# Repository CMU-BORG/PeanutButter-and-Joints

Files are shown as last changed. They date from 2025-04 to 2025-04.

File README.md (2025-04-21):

# PeanutButter-and-Joints
Paper: "PB&J: Peanut Butter and Joints for Damped Articulation"

An open-source, low-cost, biomimetic robotic grasper platform modeled on the human hand, incorporating the effects of viscoelastic joint mechanics.

An archived version of this repository is available through Zenodo:  

Authors:

* Avery S. Williamson<sup>+</sup>
* Michael J. Bennington<sup>+</sup>
* Ravesh Sukhnandan<sup>+</sup>
* Mrinali Nakhre
* Yeumin Mao
* Victoria A. Webster-Wood

<i>All authors are affiliated with Carnegie Mellon University</i>

+: These authors contributed equally to this manuscript.

This repository serves as the home for the open-source Peanut Butter and Joints biomimetic robotic grasper. The design, modeling, and characterization of this grasper is detailed in the manuscript references above. This repository contains the design files (SolidWorks part and assembly files, STLs for 3D printed components, and engineering drawings (limited) ), simulation files and associated code, and experimental data associated with the above manuscript. 

> [!NOTE]
> If you are interesting in utilizing or modifying this grasper or any of its subcomponents for your own <i>in roboto</i> investigations of human like grasping or robotic grasper development, please cite using the following DOI:
>  
> <b>Above will to be updated with correct DOI upon publication</b>
>
> Williamson, Bennington, and Sukhnandan, <i>et al.</i>, "PB&J: Peanut Butter and Joints for Damped Articulation." (2025).

## Overview:

The files in the repository are organized into three subdirectories:

- Arduino Controller

- CAD

- Modeling and Experimental Data

### Directory: [Arduino Controller](https://github.com/CMU-BORG/PeanutButter-and-Joints/tree/main/Arduino%20Controller)
This directory contains a folder entitled "Code Files" which hold all files required to implement the position controller described in the manuscript. 
 - "DCMotor.cpp" and "DCMotor.h" are library files which provide code to interface with the motor that actuates the hand.
 - "handrobot.ino" is the main Arduino/Teensy code file that implements the controller and can be used to conduct the ball drop tests.
 
### Directory: [CAD](https://github.com/CMU-BORG/PeanutButter-and-Joints/tree/main/CAD)
This directory contains the SolidWorks part files, STL files, and engineering drawings associated with the grasper and its various subcomponents. Each of these folders is further organized by the subsystem to which the files belong.
 - "Hand:" files associated with the 3D printed hand, including the palm, phalanges, and encoder mounts.
 - "Damper:" files associated with the concentric ring viscous damper (peanut butter not included)
 - "Hand Stand:" files associated with the experimental test stand used to folder the grasper in place during drop tests.
 - "Ball Stand:" files associated with the experimental test stand use to hold the ball servo and laser distance sensor used during ball drop tests.
 - "Misc:" miscellanious files associated with other components of the hand (e.g., molds for casting silicone components) and experimental setups (e.g., the pendulum joints).
Note: not all sub-components appear in all three subdirectories.

### Directory: [Modeling and Experimental Data](https://github.com/CMU-BORG/PeanutButter-and-Joints/tree/main/Modeling%20and%20Experimental%20Data)
This directory contains all files and code associated with the modeling and characterization of the grasper and its subcomponents. This directory is broken down by the associated model/characterization experiments performed. There are subfolders for:
 - Concurrent Flexion testing
 - Couette Flow Damper Modeling and the associated design parameter sweeps
 - Pendulum Damper Modeling and the associated pendulum drop test videos and Tracker files
 - Simulink Hand Modeling 
 
#### Sub-directory: [Concurrent Flexion](https://github.com/CMU-BORG/PeanutButter-and-Joints/tree/main/Modeling%20and%20Experimental%20Data/Concurrent%20Flexion) 
File List:
 - CompareFlexion.m: MATLAB script to perform range-of-motion normalized comparisons between finger flexion with and without a parallel elastic element. This script also calculates the associated pair-wise correlation coefficients reported in the manuscript.
 - Tracking Data Flexion.xlsx: position tracking data from videos of flexion experiments with and without a parallel elastic element.
 
#### Sub-directory: [Couette Flow Damper Modeling](https://github.com/CMU-BORG/PeanutButter-and-Joints/tree/main/Modeling%20and%20Experimental%20Data/Couette%20Flow%20Damper%20Modeling) 
File List:
 - Effective_Damping_Coeff_v2.m: MATLAB function that calculated the effective damping coefficient (G) for a given input geometry for the concentric cylinder damper
 - Parameter_Sweeps_v2.m: MATLAB script that performs the parametric sweeps of the damper design space and calculates the heatmaps of effective damping coefficients.
 - PlotFins.m: MATLAB function to plot the cross-section of the concentric ring dampers for visualization.
 
#### Sub-directory: [Pendulum Damper Modeling](https://github.com/CMU-BORG/PeanutButter-and-Joints/tree/main/Modeling%20and%20Experimental%20Data/Pendulum%20Damper%20Modeling)
Folder List:
 - 20250414_Parameter: folder containing the final distributions for the friction and damping parameters resulting from the bootstrapping method.
 - No Damper Pendulum Tests: folder containing the videos, Tracker files, and resulting positional data from the pendulum drop tests without a viscous damper
 - Peanut Butter Damper Pendulum Tests: folder containing the video of all drop experiments, the Tracker file, and resulting data. All experiments are within the single video
 
File List:
 - AllTrialError.m: MATLAB function that calculates the error between the pendulum model and a set of experimental data for a given parameter set. Used to calculate the objective function in the optimization.
 - dynamics.m: MATLAB function that calculated the model angular acceleration for a given position, velocity, and set of parameters.
 - PB_J__Parameter_Estimation.pdf: Text document explaining the details of the parameter estimation routine.
 - Pendulum_ParameterEstimation.m: MATLAB script that conducts the bootstrap parameter estimation of the frictional and damping parameters from the pendulum drop tests. To rerun the Monte Carlo simulations to obtain the average mdoel results, set the "if_save_friction" and "if_save_damping" parameters to 0. This will reload the saved parameters from the folder listed above. If you want to rerun the optimization, set these variables to 1. <b>Important!:</b> Before you run the optimization, create a new save folder and update the "outfolder" variables or else you will overwrite the results. Additionally, the optimization is slow and you should expect it to take many hours. It is best to let it run overnight.
 - theta_model.m: MATLAB function that returns a vector of model angles for a given set of parameters and initial conditions. These values are calculated by integrating the presented dynamical model and linearly reinterpolating at a set of time points that align with the experimental data time points.
 
#### Sub-directory: [Simulink Hand Modeling](https://github.com/CMU-BORG/PeanutButter-and-Joints/tree/main/Modeling%20and%20Experimental%20Data/Simulink%20Hand%20Modeling)
Folder List:
 - CAD: holds the CAD files of the hand used as the geometry of the hand model
 - slprj: autogenerated folder from Simulink.
 
File List: 
 - CatchingBall.avi/.mp4: video files showing the simulation successfully capturing a ball. The kinematics of these simulations is shown in the manuscript.
 - HandDynamicsModel.slx: Simulink model utilizing Simscape Multibody to simulate the dynamics of the hand, the forces transmission of the pulleys, and the contact interactions with the ball.
 - InitTestParams.m: MATLAB script that initializes the simulation paramters for the Simulink model. This script must be run before the Simulink model can be run.
 - PlotResults.m: Script to plot the results of the Simulink simulations and generate the figure presented in the manuscript. This script can be run after the Simulink simulation is complete.

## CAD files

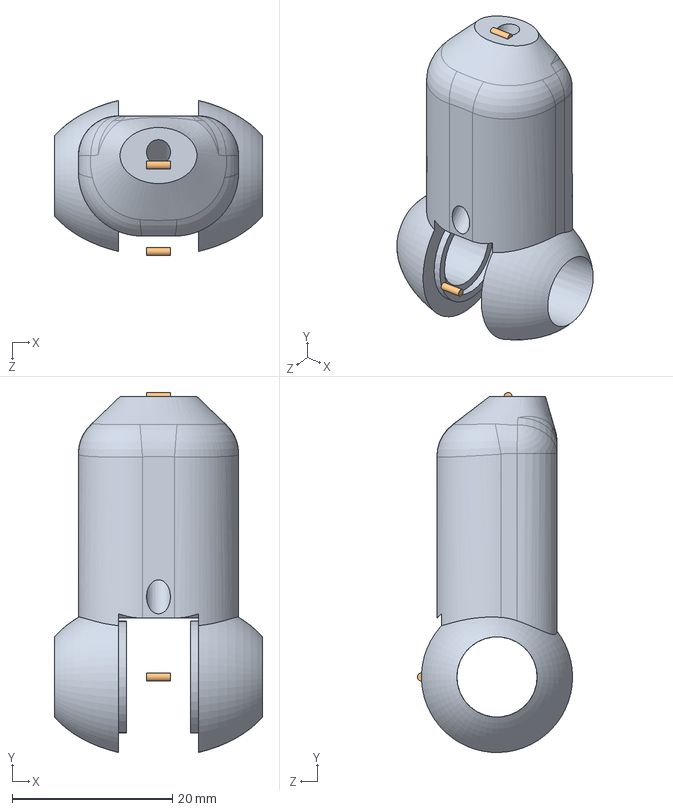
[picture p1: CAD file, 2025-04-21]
Modeling and Experimental Data/Simulink Hand Modeling/CAD/TipWithRollers.SLDASM
26.0 x 44.9 x 19.4 mm
tip
FauxAxle x 3

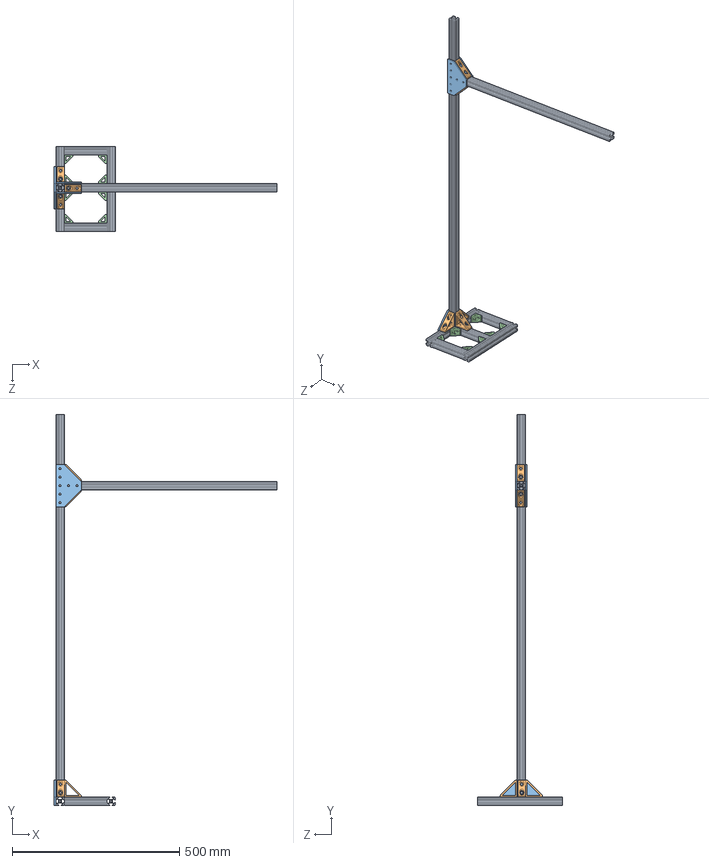
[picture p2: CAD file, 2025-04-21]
CAD/SolidWorks Parts and Assemblies/Ball Stand/stand_assembly.SLDASM
665.2 x 1168.4 x 254.0 mm
T_slot x 7
connector_big x 5
connector_plate2 x 3
connector_small x 8

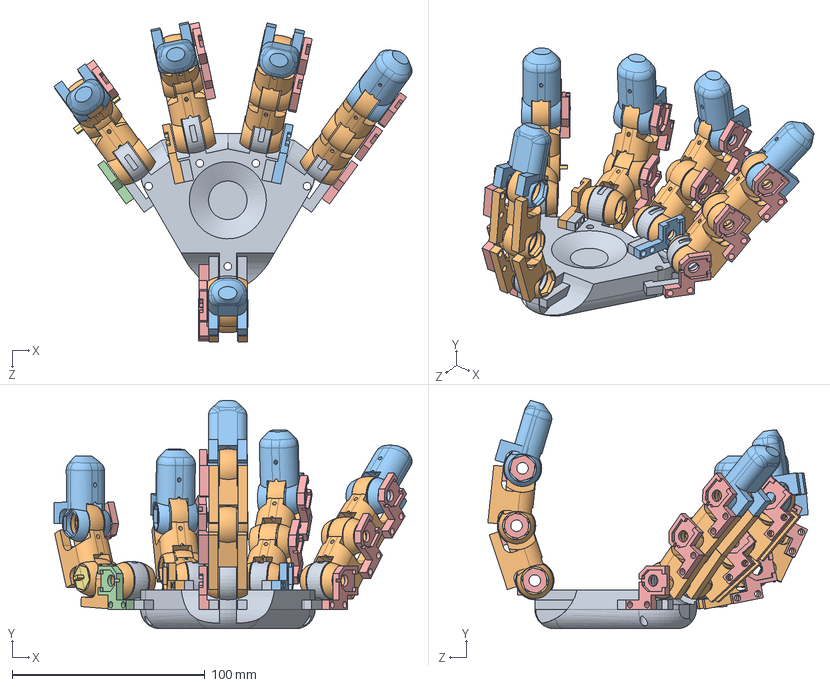
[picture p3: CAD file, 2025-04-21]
CAD/SolidWorks Parts and Assemblies/Hand/hand.SLDASM
185.9 x 118.6 x 166.4 mm
palm
digit x 10
tip x 5
encoder mount left
encoder mount right x 11
BoreRode
EndCap_hex x 2
Inner Fin x 6
InnerKey_hex
encoder mount center left
encoder mount center right

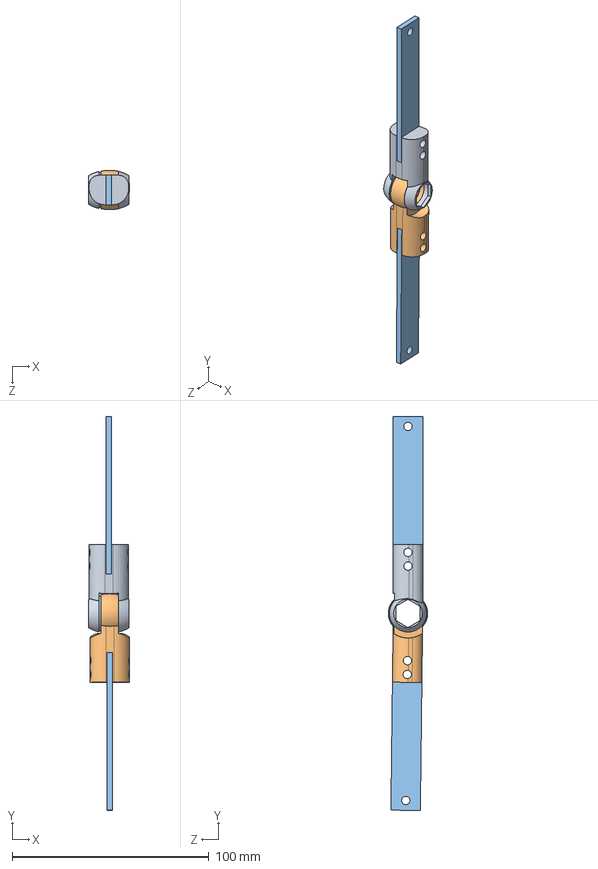
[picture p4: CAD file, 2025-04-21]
CAD/SolidWorks Parts and Assemblies/Misc/Pendulum.SLDASM
20.8 x 200.1 x 20.0 mm
Top
Bottom
Bar x 2

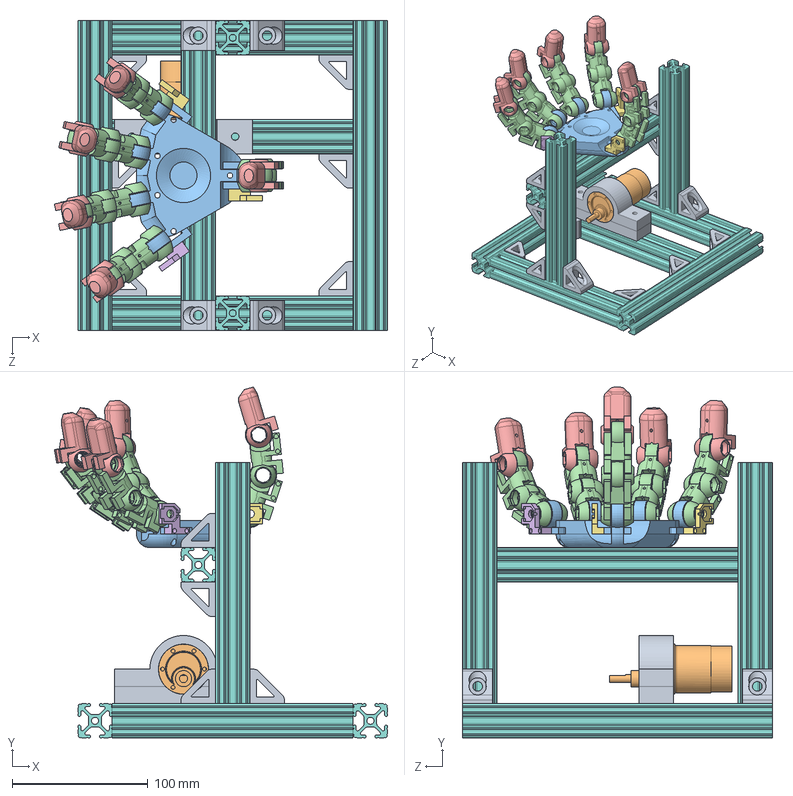
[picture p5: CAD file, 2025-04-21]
CAD/SolidWorks Parts and Assemblies/Hand Stand/hand_stand_assembly.SLDASM
245.9 x 259.0 x 228.6 mm
motor_hold_down x 2
pololu_37D
palm
digit x 10
tip x 5
encoder mount left
encoder mount right x 2
T_slot x 8
connector_small x 14

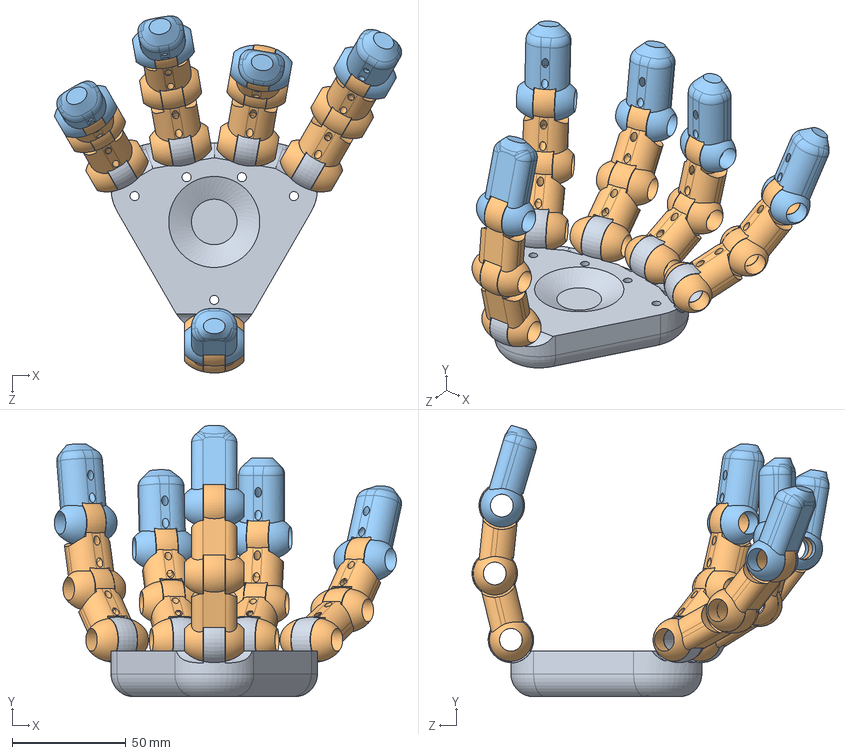
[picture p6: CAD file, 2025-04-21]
Modeling and Experimental Data/Simulink Hand Modeling/CAD/hand.SLDASM
152.5 x 119.3 x 156.8 mm
palm
digit x 10
tip x 5

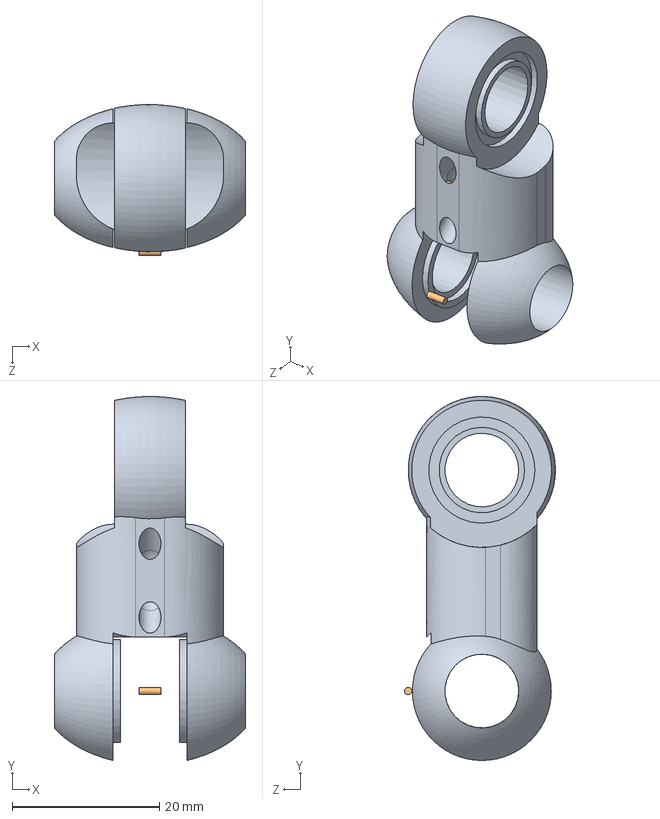
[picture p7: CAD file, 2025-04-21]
Modeling and Experimental Data/Simulink Hand Modeling/CAD/DigitWithRollers.SLDASM
26.0 x 49.4 x 20.5 mm
digit
FauxAxle x 3

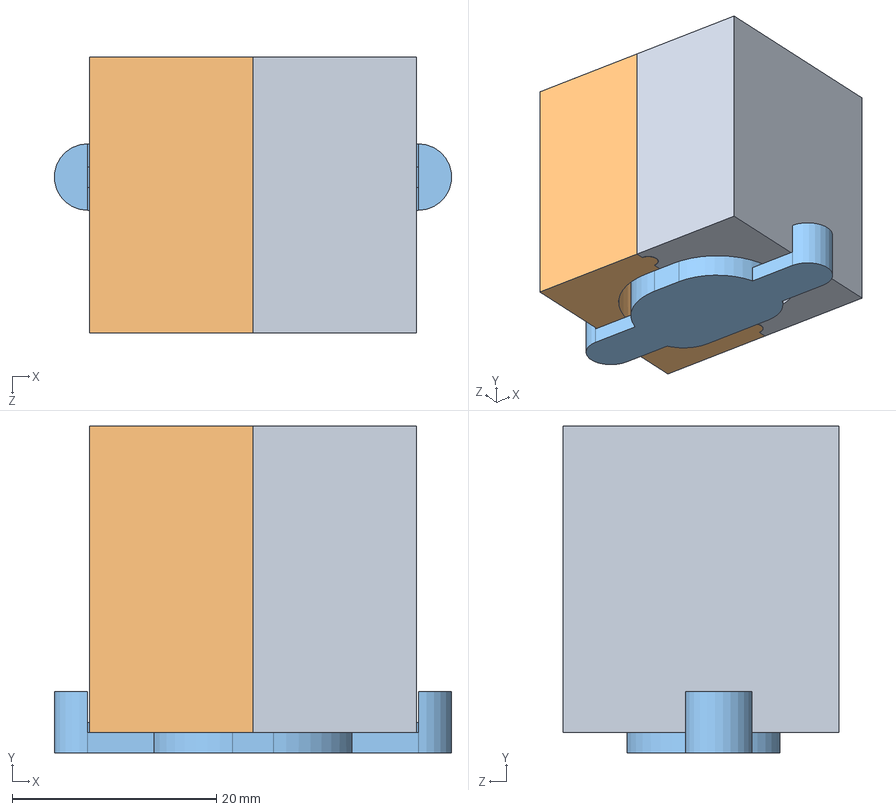
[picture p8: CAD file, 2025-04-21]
CAD/SolidWorks Parts and Assemblies/Misc/FingerTipMold.SLDASM
38.9 x 32.0 x 27.0 mm
TipMoldLeft
TipMoldRight
Tip_mold_Cap

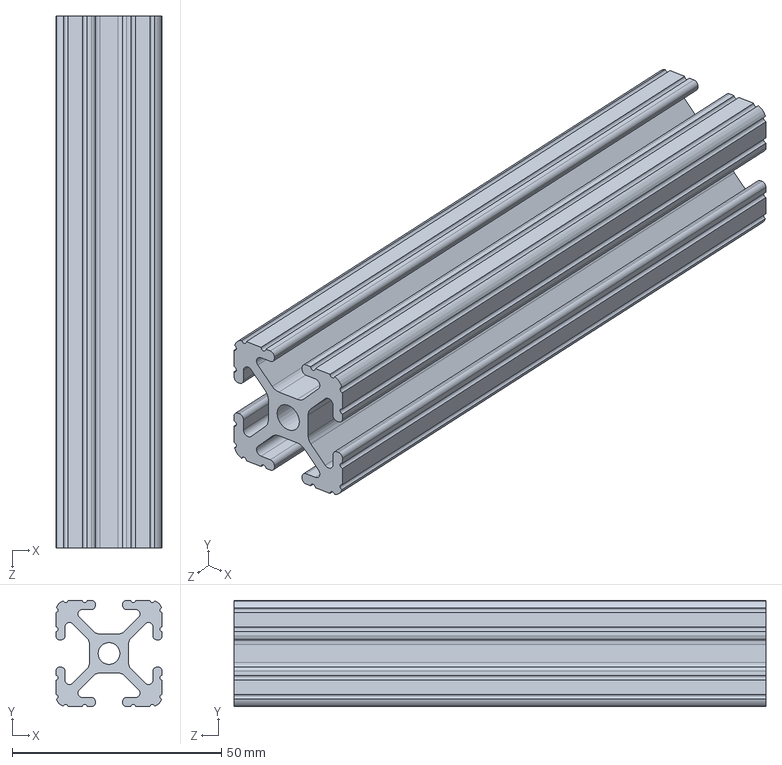
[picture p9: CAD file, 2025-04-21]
CAD/SolidWorks Parts and Assemblies/Ball Stand/T_slot.SLDPRT
25.4 x 25.4 x 127.0 mm

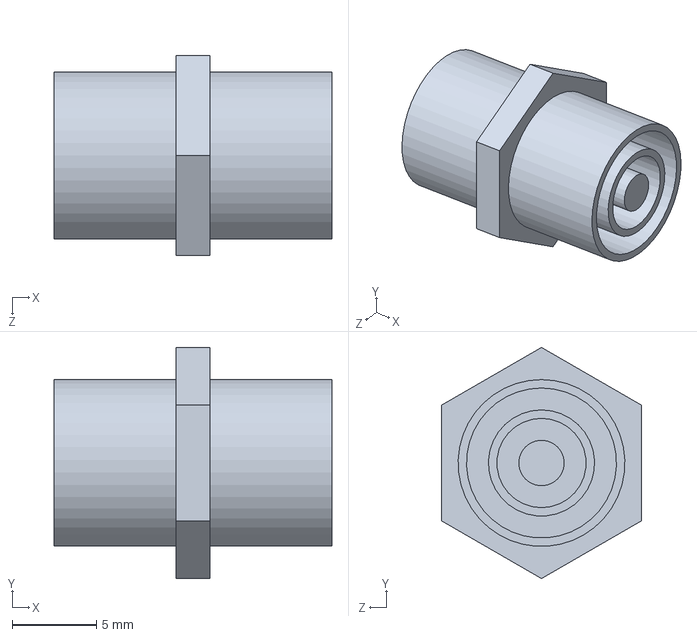
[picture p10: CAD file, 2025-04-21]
CAD/SolidWorks Parts and Assemblies/Damper/Inner.SLDPRT
16.5 x 13.7 x 11.9 mm

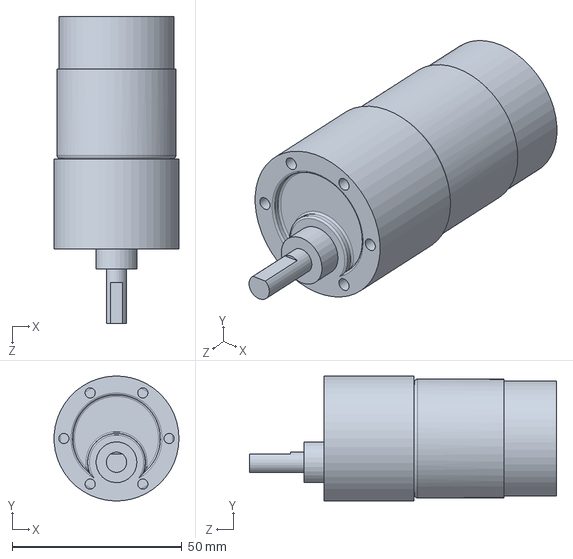
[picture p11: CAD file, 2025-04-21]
CAD/SolidWorks Parts and Assemblies/Hand Stand/pololu_37D.SLDPRT
36.8 x 36.8 x 90.4 mm

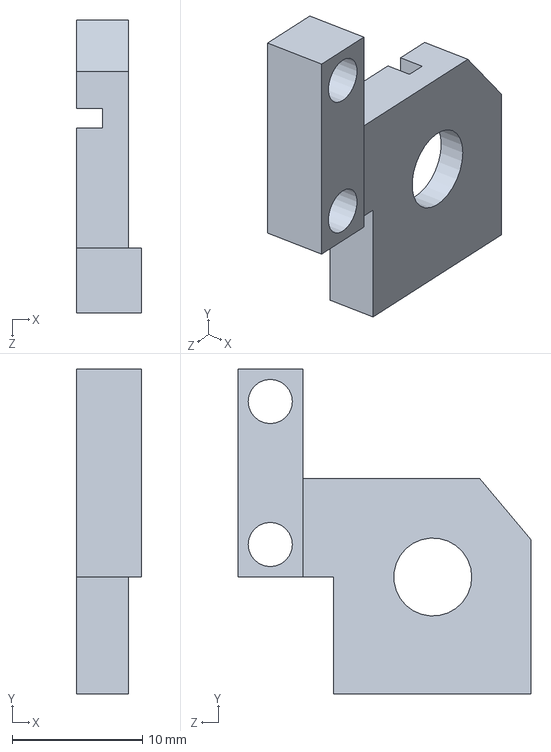
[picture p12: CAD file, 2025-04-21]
CAD/SolidWorks Parts and Assemblies/Hand/encoder mount left.SLDPRT
5.00 x 25.0 x 22.6 mm

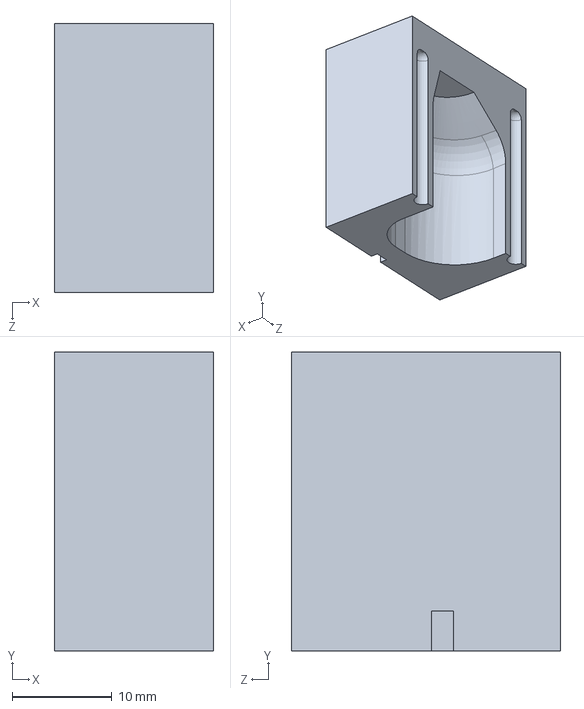
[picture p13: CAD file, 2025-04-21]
CAD/SolidWorks Parts and Assemblies/Misc/TipMoldRight.SLDPRT
16.0 x 30.0 x 27.0 mm

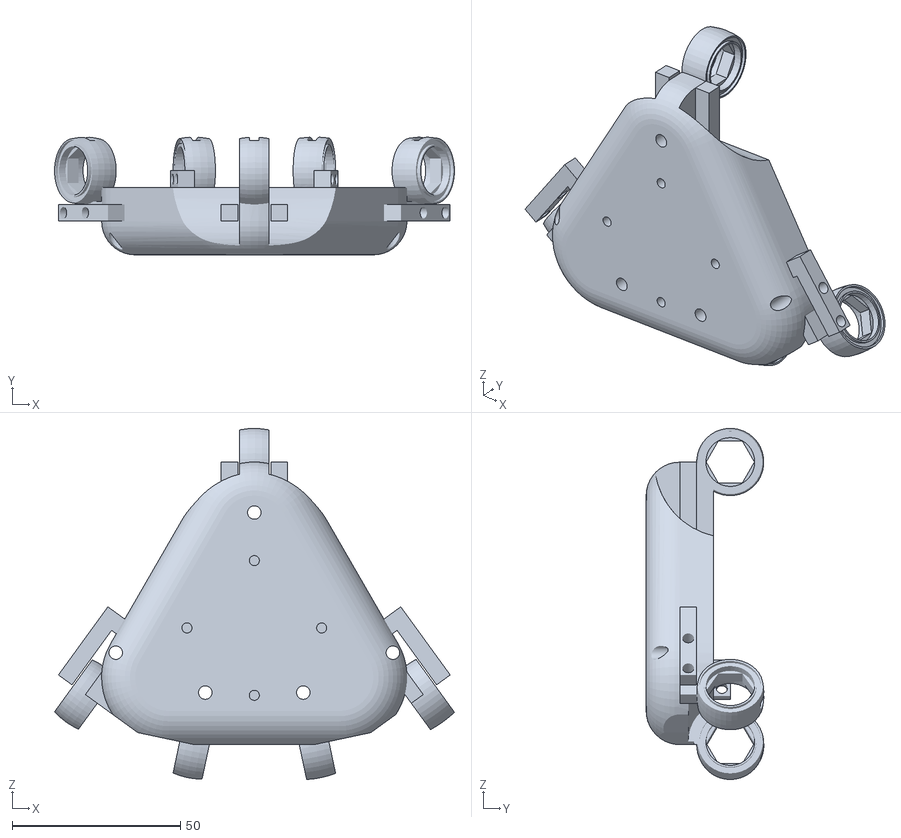
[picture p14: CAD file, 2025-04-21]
CAD/STLs/Hand/palm.STL
118.8 x 35.0 x 104.3

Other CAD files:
CAD/SolidWorks Parts and Assemblies/Damper/Concentric Damper.SLDASM
CAD/STLs/Dampers/Inner.STL
CAD/STLs/Misc/Tip_mold_Cap.STL
Modeling and Experimental Data/Simulink Hand Modeling/CAD/digit.STEP
CAD/Drawings/Hand/digit.SLDDRW
CAD/Drawings/Hand/encoder mount center left.SLDDRW
CAD/Drawings/Hand/palm.SLDDRW
CAD/Drawings/Hand/tip.SLDDRW
CAD/STLs/Dampers/Outer.STL
CAD/STLs/Hand/digit.STL
CAD/STLs/Hand/encoder mount center left.STL
CAD/STLs/Hand/encoder mount center right.STL
CAD/STLs/Hand/encoder mount left.STL
CAD/STLs/Hand/encoder mount right.STL
CAD/STLs/Hand/encoder mount.STL
CAD/STLs/Hand/tip.STL
CAD/STLs/Misc/TipMoldLeft.STL
CAD/STLs/Misc/TipMoldRight.STL
CAD/STLs/Misc/Tip_mold_Cap_v2.STL
CAD/SolidWorks Parts and Assemblies/Ball Stand/connector_big.SLDPRT
CAD/SolidWorks Parts and Assemblies/Ball Stand/connector_plate2.SLDPRT
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

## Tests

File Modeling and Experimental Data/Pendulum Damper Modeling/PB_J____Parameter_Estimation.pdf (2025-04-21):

# PB&J: Peanut Butter and Joints for Damped Articulation - Parameter Estimation Protocol

### April 21, 2025

The parameters of the joint damping model (µk, µd, and b) were fit to experimental angular position data from pendulum drop tests using a bootstrapping method. These pendulum drop tests are described in our main manuscript. µk and µd were simultaneously fit to data from experiments without the damper, and then, given those parameters, b was fit to data from experiments with the damper.
To fit the frictional parameters: For a single iteration, the following algorithm was used:
1. Sample (with replacement) 5 dataset from the 15 no-damper experiments.
2. Sample an initial condition for µk and µd from a uniform distribution over the range [0, 1e − 2] and [0, 1e − 5] respectively.
3. Minimize the objective function ϕ1 for both parameters using fminsearch.

The objective function ϕ was the total squared error across all five experiments, modified by penalty terms that penalize negative parameters:

ϕ1(µ) = X

5
i=1 X

j

((θ

data
j − θ

model
j

(µ))²
)

!
+ (10⁹
)

(µ < 0)
(1)

where µ = [µk, µd]. θ

model
j

(µ) was found by integrating the equation of motion from Appendix B of our manuscript. The initial model state was determined from the corresponding dataset. Because the model had a higher temporal resolution than the data, the model output was reinterpolated at the dataset time points. This procedure was repeated for N = 300 iterations to obtain distributions on µk and µd.
To fit the damping parameter: At each iteration:
1. Sample (with replacement) 5 dataset from the 15 no-damper experiments.
2. Sample a value of µ from the obtained parameter distribution.

1

26 | 3. Sample an initial condition for b from a uniform distribution over the range [0, 1e5].
27 | 4. Minimize the objective function ϕ2 for b using fminsearch.
28 | The objective function ϕ2 was of the same form as ϕ1 except that it was parameterized by
29 | b. To account for the variability introduced by randomly sampling the frictional coefficients,
30 | this procedure was repeated for N = 3000 iterations. The resampled µk and µd were saved
31 | for each value of b to obtain the full joint distribution of parameters.

2

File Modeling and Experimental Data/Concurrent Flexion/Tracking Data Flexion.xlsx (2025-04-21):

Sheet: With Elastic Stiffness
t | x | y | θ | t | x | y | θ | t | x | y | θ | theta1 | theta2 | theta3 | q1 | q2 | q3
0 | -240.6648 | 31.91136 | 172.4468 | 0 | -518.076 | 85.05736 | 170.6764 | 0 | -0.08200875 | 0.01781797 | 167.7419 | 7.5532 | 9.3236 | 12.2581 | 0 | 1.7704 | 2.9345
0.01668333 | -240.6473 | 31.87291 | 172.4553 | 0.01668333 | -517.9738 | 84.9605 | 170.685 | 0.01668333 | -0.08200101 | 0.01780988 | 167.7462 | 7.5447 | 9.315 | 12.2538 | -0.0085 | 1.7703 | 2.9388
0.03336667 | -240.6583 | 31.87292 | 172.4556 | 0.03336667 | -518.071 | 85.04521 | 170.6776 | 0.03336667 | -0.08200401 | 0.01781227 | 167.745 | 7.5444 | 9.3224 | 12.255 | -0.0088 | 1.778 | 2.9326
0.05005 | -240.655 | 31.89892 | 172.4494 | 0.05005 | -518.0301 | 84.97671 | 170.6843 | 0.05005 | -0.08200465 | 0.01781312 | 167.7446 | 7.5506 | 9.3157 | 12.2554 | -0.0026 | 1.7651 | 2.9397
0.06673333 | -240.6587 | 31.90551 | 172.448 | 0.06673333 | -518.0625 | 85.02337 | 170.6798 | 0.06673333 | -0.08200589 | 0.01781511 | 167.7434 | 7.552 | 9.3202 | 12.2566 | -0.0012 | 1.7682 | 2.9364
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

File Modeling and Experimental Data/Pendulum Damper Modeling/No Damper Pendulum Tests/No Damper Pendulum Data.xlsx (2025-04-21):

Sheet: Trial 1
t | x | y | theta | theta (deg) | t_true
0 | -276.4041 | -238.443 | 2.282594908 | 130.7830546 | 0
0.004166667 | -275.5904 | -239.3831 | 2.286000947 | 130.9782063 | 0.000520833375
0.008333333 | -275.7616 | -239.415 | 2.285759471 | 130.9643707 | 0.001041666625
0.0125 | -276.0972 | -239.0743 | 2.284452632 | 130.8894943 | 0.0015625
0.01666667 | -275.0051 | -239.5815 | 2.287463972 | 131.0620314 | 0.00208333375
0.02083333 | -274.267 | -241.5213 | 2.292792875 | 131.367355 | 0.00260416625
0.025 | -272.8027 | -242.0004 | 2.296432571 | 131.5758943 | 0.003125
0.02916667 | -271.6822 | -244.2923 | 2.303160443 | 131.9613729 | 0.00364583375
0.03333333 | -269.6986 | -245.9055 | 2.310081139 | 132.3578996 | 0.00416666625
0.0375 | -267.6559 | -247.5844 | 2.317258568 | 132.769136 | 0.0046875
0.04166667 | -265.7168 | -249.5182 | 2.324765596 | 133.199257 | 0.00520833375
0.04583333 | -263.6213 | -252.0157 | 2.333690983 | 133.710644 | 0.00572916625
0.05 | -260.9883 | -254.4234 | 2.343457983 | 134.2702519 | 0.00625
0.05416667 | -258.2004 | -257.3752 | 2.35459395 | 134.9082958 | 0.00677083375
0.05833333 | -254.5977 | -260.56 | 2.367767711 | 135.6630967 | 0.00729166625
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

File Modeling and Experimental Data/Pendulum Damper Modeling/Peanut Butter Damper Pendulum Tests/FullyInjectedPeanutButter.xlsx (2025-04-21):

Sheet: Trial 1
t | x | y | theta | theta (deg) | t
0 | -343.5896 | -306.5982 | 2.299362348 | 131.7437581 | 0.6666667
0.0041666625 | -337.1517 | -313.664 | 2.320120513 | 132.9331134 | 0.7
0.008333325 | -330.959 | -319.825 | 2.339087564 | 134.0198453 | 0.7333333
0.0125 | -323.1158 | -327.6207 | 2.363117151 | 135.3966392 | 0.7666667
0.0166666625 | -315.9018 | -334.525 | 2.384818946 | 136.6400605 | 0.8
0.020833325 | -308.0233 | -341.7716 | 2.408084716 | 137.973091 | 0.8333333
0.025 | -298.958 | -349.4592 | 2.43392139 | 139.4534233 | 0.8666667
0.0291666625 | -290.0626 | -356.6638 | 2.458814771 | 140.879709 | 0.9
0.033333325 | -280.9799 | -363.8054 | 2.483949268 | 142.3198096 | 0.9333333
0.0375 | -270.8253 | -371.3608 | 2.511485993 | 143.8975477 | 0.9666667
0.0416666625 | -260.0759 | -378.6663 | 2.539766645 | 145.5179097 | 1
0.0458332875 | -249.1113 | -385.783 | 2.568225702 | 147.1484936 | 1.033333
0.0500000375 | -237.9874 | -392.5485 | 2.596581159 | 148.7731416 | 1.066667
0.0541666625 | -226.959 | -398.741 | 2.624136443 | 150.3519431 | 1.1
0.0583332875 | -214.0615 | -405.5916 | 2.655971974 | 152.1759846 | 1.133333
0.0625000375 | -201.997 | -411.531 | 2.68529766 | 153.8562226 | 1.166667
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

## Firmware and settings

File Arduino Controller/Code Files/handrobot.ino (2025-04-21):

#include "DCMotor.h"

long startTime;

typedef enum {
  FORWARD,
  BACKWARD,
  INPUTWAIT,
  PULL_I,
  PULL,
  STOP
} robotStates_e;

robotStates_e state = INPUTWAIT;

DCMotor motor(33, 34, 31, 32,
              0.5, 0, 0,
              0.5, 1000, 80);

void setup() {
  Serial.begin(38400);
  motor.setup();
  pinMode(14, INPUT);
}

void loop() {
  // int reading = analogRead(14);
  // Serial.println(reading);

  // motor.setSpeed(100);
  // delay(50);
  // motor.setSpeed(200);
  // delay(50);
  // motor.setSpeed(0);
  // delay(50);
  // motor.setSpeed(200);
  // delay(50);
  // motor.setSpeed(100);
  // delay(50);
  // encData enc = motor.getPos();
  // Serial.println(enc.val);
  // delay(50);
  robotStates_e nextState = state;
  Serial.println(state);
  switch(state) {
    case INPUTWAIT:
      motor.setSpeed(0);
      if (Serial.available()) {
        int a = 0;
        while (a != -1) {
          a = Serial.read();
        }
        nextState = PULL_I;
      }
      break;
    case PULL_I:
      motor.setSpeed(100);
      startTime = millis();
      nextState = PULL;
      break;
    case PULL:
      if (millis() - startTime > 2000) {
        Serial.print(startTime);
        Serial.print(" ");
        nextState = INPUTWAIT;
      }
      break;
    case STOP:
      motor.setSpeed(0);
      break;
  }
  state = nextState;
  delay(10);
}

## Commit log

2025-04-21 Initial Commit
    This commit contains all files associated with this manuscript. Subsequent commits will be to updated comments and files, but will not contain additional design/modeling work.
    [Bar.SLDPRT, Bottom.SLDPRT, Concentric Damper.SLDASM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]
2025-04-21 Simulink Model and Final Comments
    Added the simulink model files. Updated all code files to have sufficient comments. Updated the README file with the updated file descriptions.
    [DigitWithRollers.SLDASM, FauxAxle.SLDPRT, TipWithRollers.SLDASM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]
2025-04-21 Updated names and uploaded drawings
    See title.
    [digit.SLDDRW, encoder mount center left.SLDDRW, palm.SLDDRW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]
